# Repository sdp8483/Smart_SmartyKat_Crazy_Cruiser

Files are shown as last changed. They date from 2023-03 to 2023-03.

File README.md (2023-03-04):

# Smart SmartyKat Toy
## Modifying the SmartyKat Crazy Cruiser to be smarter about battery consumption

The Crazy Cruiser cat toy by SmartyKat is not so smart. The toy is the cat equivalent of a simple bristle bot. It consists of a power switch, LED, and vibration motor all powered by two LR44 coin cells. To activate the toy for cat play time a human is required to turn the toy on. During playtime it runs at a constant vibration speed and the light doesn't even blink! Not that smart. This also means that when kitty gets tired of playing (if a kitten can get tired please let me know) the toy will continue to run and drain the batteries. I aim to fix that by making the toy smarter.

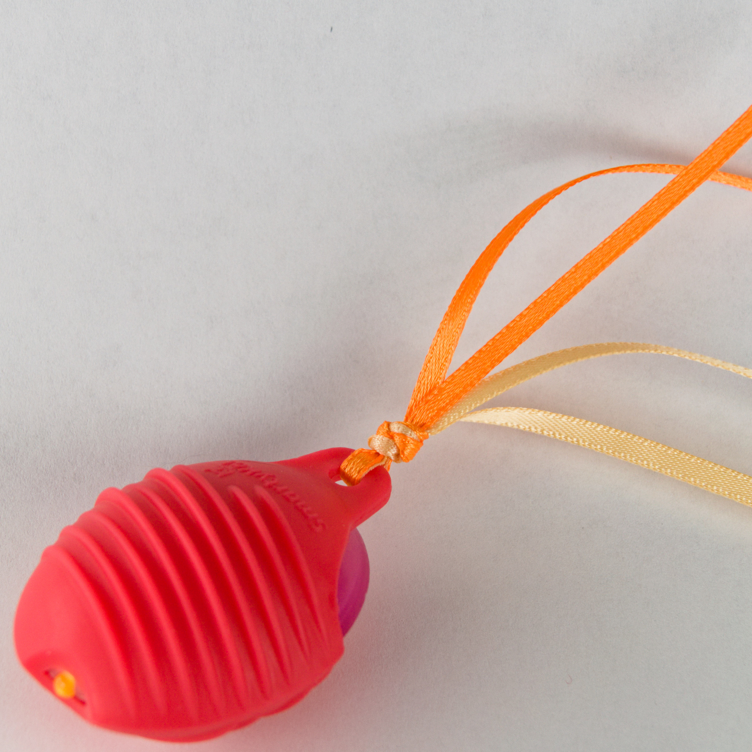
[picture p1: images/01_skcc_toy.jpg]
SmartyKat Toy


Simple and minimal parts will be used to smarten up this toy, after all it is still a low cost cat toy. This will be accomplished by adding a vibration switch and a microcontroller. The vibe switch will be used to wake up the uC from deep low power sleep in which the uC will start the vibration motor and LED. The toy will then remain active for a set amount of time then turn off to be activated later.

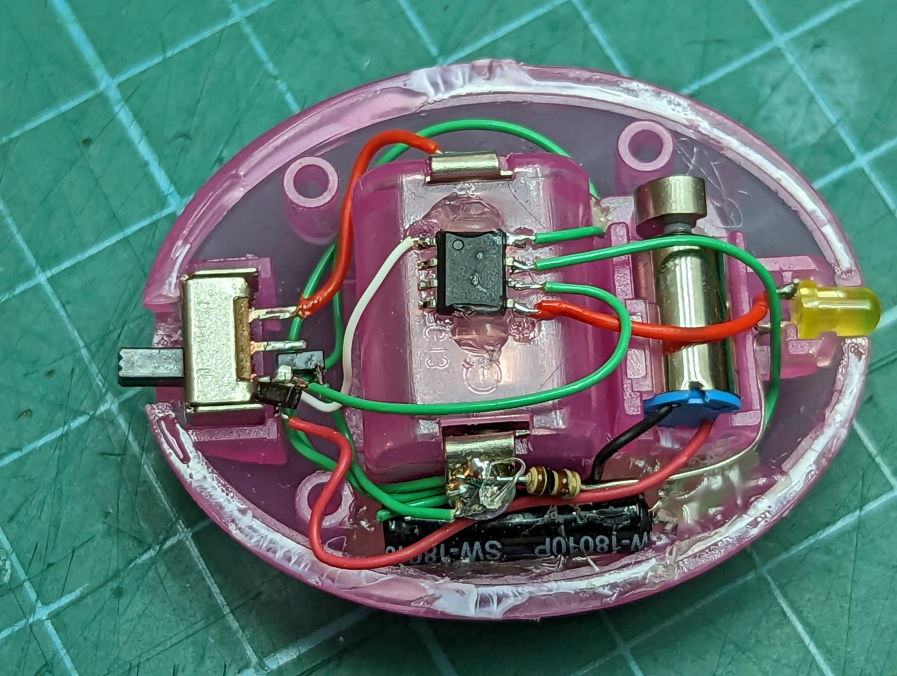
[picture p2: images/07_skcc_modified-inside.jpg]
Modified Toy


For more info see: https://samueldperry.com/2023/03/04/smart-smartykat-toy/

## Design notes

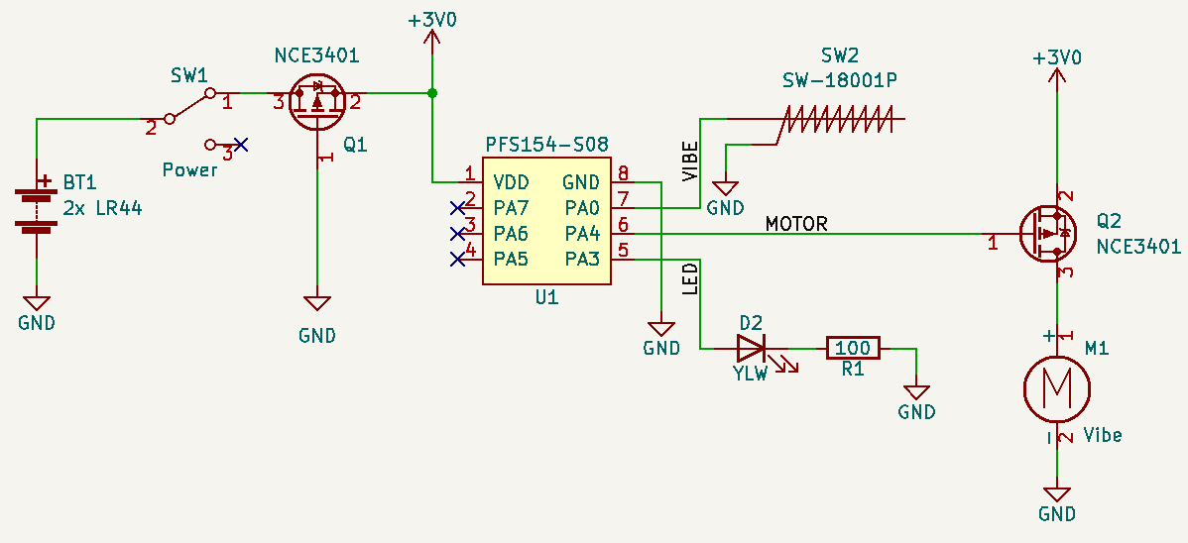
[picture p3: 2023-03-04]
pcb/images/skcc_schematic.png

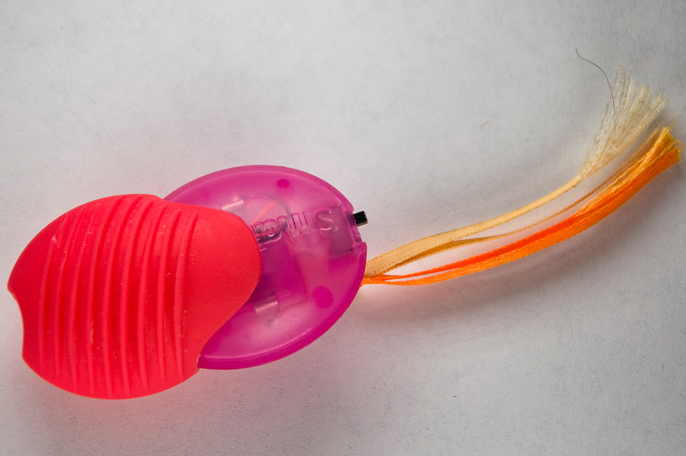
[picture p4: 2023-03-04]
images/02_skcc_toy.jpg

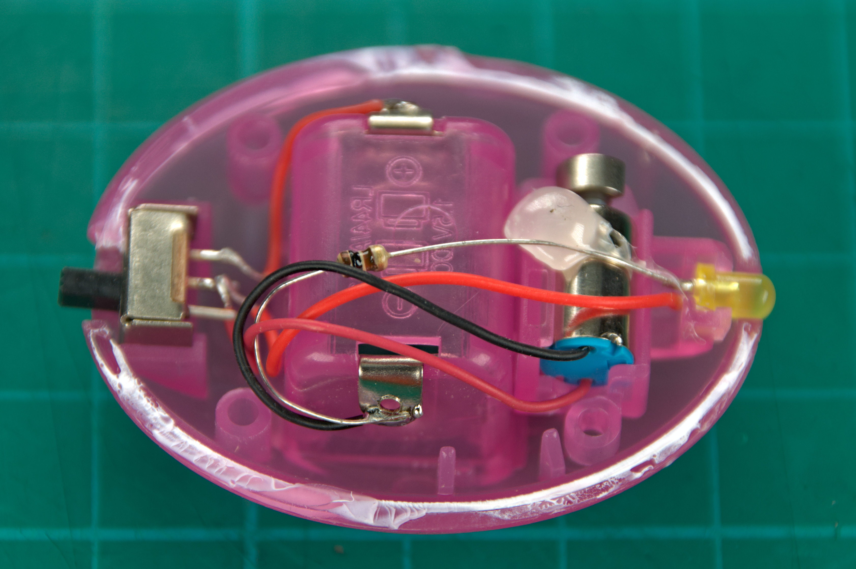
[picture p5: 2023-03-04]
images/03_skcc_stock-inside.jpg

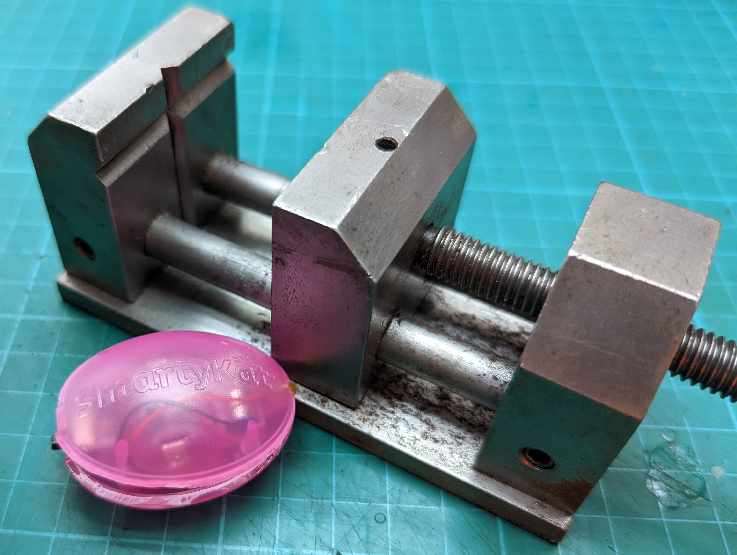
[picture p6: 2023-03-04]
images/04_skcc_craked-open.jpg

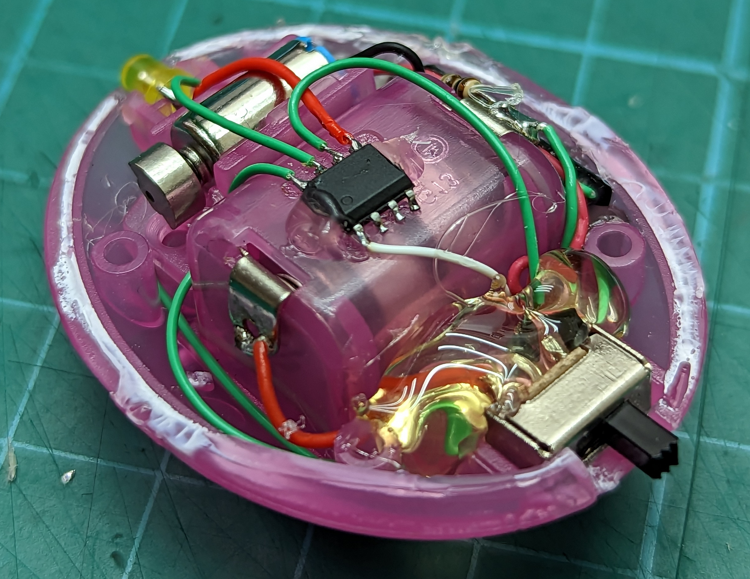
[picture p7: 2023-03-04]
images/08_skcc_hot-snot.jpg

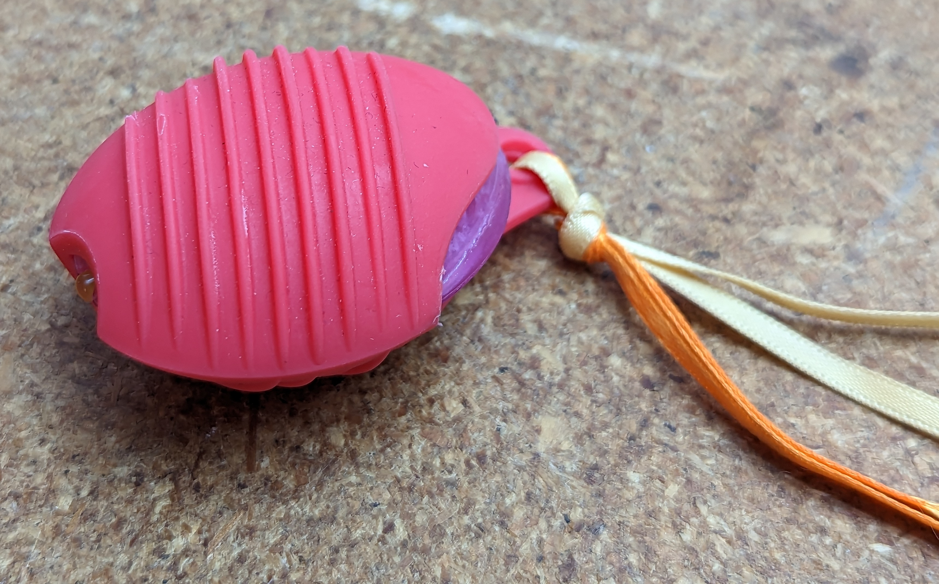
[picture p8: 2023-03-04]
images/09_skcc_done.jpg

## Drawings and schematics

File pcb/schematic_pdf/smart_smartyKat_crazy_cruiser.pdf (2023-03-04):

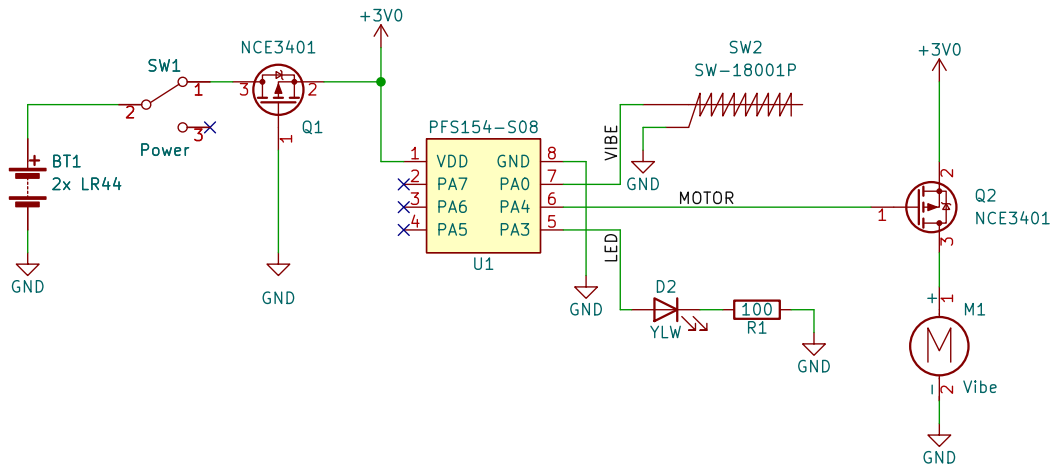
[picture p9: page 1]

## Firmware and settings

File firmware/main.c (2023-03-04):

/* Smart SmartyKat Crazy Cruiser
 * Target Device: PFS154-S08
 * 
 * Sam Perry 2023
 * github.com/sdp8483/Smart_SmartyKat_Crazy_Cruiser
 */

#include <stdint.h>
#include <pdk/device.h>
#include "auto_sysclock.h"

// Pin Defines - all pins are on port A
#define VIBE_PIN              0     /* vibration sensor input pin, used to wake from deep sleep */
#define MOTOR_PIN             4     /* motor control pin, controlled with a pmosfet */
#define LED_PIN               3     /* LED output pin, current source */

// Output Pin Fuction Defines
#define LED_ON()              PA |= (1 << LED_PIN)
#define LED_OFF()             PA &= ~(1 << LED_PIN)
#define LED_TOGGLE()          PA ^= (1 << LED_PIN)
#define MOTOR_ON()            PA &= ~(1 << MOTOR_PIN)
#define MOTOR_OFF()           PA |= (1 << MOTOR_PIN)


// Toggle the motor on and off to give toy some character using profiles
#define MAX_TICKS             64    /* go to sleep after this many ticks */
uint8_t tick = 0;                   /* tick count, number of T16 interrupts since starting T16 */
#define NUM_PROFILES          8     /* number of profiles, a new one is played each wake event to give more character */
uint64_t profile[NUM_PROFILES] = {0b1100110011001111111111000000000010101010101010101010111111111111,
                                  0b1111111111111111111111111111111111111111111111111111111111111111,
                                  0b1100110011001100110011001100110011111111111111111111111111111111,
                                  0b1111111111001111001111001111001111001111001111001111001111001111,
                                  0b0101010101010101010101010101010101010101010101010101010101010101,
                                  0b1111001110011100111001110011100111001110011100111001110011100111,
                                  0b1110111000000111000000000000000011111111111111111111111111111111,
                                  0b1110101010101010000000001111111101010101000000001111111101010101};
                                    /* motor will be turned on when bit is 1 and off when bit is 0 
                                       this playback profile is backwards */
uint8_t profile_i = 0;              /* profile number to playback, increments each wake */

// State Machine
typedef enum {
  GOTO_SLEEP,                       /* prepare to sleep */
  SLEEP,                            /* toy is in deep sleep */
  WAKEUP,                           /* toy was awaken from deep sleep */
  TOCK,                             /* T16 calling for next profile point */
  LIGHT_SLEEP,                      /* light sleep between ticks */
} fsm_states_t;

volatile fsm_states_t fsm_state = GOTO_SLEEP;

// Function Prototypes
void settling_delay(void);          /* use timer3 as delay to wait for vibe sensor to settle */

// Service Interrupt Requests
void interrupt(void) __interrupt(0) {
  /* Some notes and thoughts about interrupts on the PFS154
   *  Section 5.7 of the datasheet contains information about the interrupt controller.
   *  When an interrupt is triggered global interrupts are disabled, ie __disgint() is automaticaly called.
   *  CPU steps into ISR function below and executes code there. When done __engint() is automaticaly called and 
   *  code execution starts in the main loop where it left off. Confusingly the datasheet says that even if INTEN = 0 
   *  INTRQ can still be triggered by the interrupt source. So the peripheral or port should be further disabled to prevent
   *  triggering. */

  if (INTRQ & INTRQ_PA0) {          /* wake pin was pulled low */
    INTRQ &= ~INTRQ_PA0;            /* mark PA0 interrupt request serviced */
    fsm_state = WAKEUP;             /* change state */
  }

  if (INTRQ & INTRQ_T16) {          /* timer has expired */
    INTRQ &= ~INTRQ_T16;            /* mark T16 interrupt request serviced */
    T16C = 0;                       /* reset timer to zero */
    fsm_state = TOCK;               /* get next profile point */
  }

  if (INTRQ & INTRQ_TM2) {          /* LED toggle timer */
    INTRQ &= ~INTRQ_TM2;            /* mark interrupt request serviced */
    fsm_state = LIGHT_SLEEP;        /* go to light sleep */
  }

  if (INTRQ & INTRQ_TM3) {          /* settling delay has expired */
    INTRQ &= ~INTRQ_TM3;            /* mark interrupt request serviced */
  }
}

// Main program
void main() {
  MISC |= MISC_FAST_WAKEUP_ENABLE;  /* enable faster wakeup, 45 ILRC clocks instead of 3000 */

  // Initialize hardware
  PADIER = 0;                       /* on reset all pins are set as wake pins, setting register to 0 to disable */
  PBDIER = 0;                       /* there is no port B on the -S08 but without setting this to 0 the uC will wake unexpectedly */

  // Set Vibration Sensor pin as input
  PAC &= ~(1 << VIBE_PIN);          /* set as input (all pins are input by default, setting to make sure) */
  PAPH |= (1 << VIBE_PIN);          /* enable pullup resistor on pin */

  // Set output pins
  PAC |= (1 << MOTOR_PIN);          /* set motor control pin as output */
  PAC |= (1 << LED_PIN);            /* set led pin as output */
  LED_OFF();                        /* set initial LED state */
  MOTOR_OFF();                      /* set initial motor state */

  // Forever Loop
  while (1) {
    switch (fsm_state) {
      case GOTO_SLEEP:
        __disgint();                /* disable global interrupts */
        
        T16M = T16M_CLK_DISABLE;    /* turn off tick timer */
        TM2C = TM2C_CLK_DISABLE;    /* stop LED toggling */
        LED_OFF();
        MOTOR_OFF();

        settling_delay();           /* delay for vibe switch to settle */

        INTEN = 0;                  /* disable all interrupts */
        PADIER = (1 << VIBE_PIN);   /* enable only one wakeup pin */
        PBDIER = 0;                 /* make sure port B does not wake */
        INTEGS |= INTEGS_PA0_FALLING;
                                    /* trigger when switch closes and pulls pin to ground */
        INTEN |= INTEN_PA0;         /* enable interrupt on wake pin */
        INTRQ = 0;                  /* reset interrupts */

        fsm_state = SLEEP;          /* change state */
        break;

      case SLEEP:
        __engint();                 /* enable global interrupts */
        __stopsys();                /* go to deep sleep */
        break;
      
      case WAKEUP:
        __disgint();                /* disable global interrupts */
        INTEN = 0;                  /* disable all interrupts */
        PADIER = 0;                 /* disable wakeup pin */
        PBDIER = 0;                 /* disable port B wake pins to be sure */

        T16M = (uint8_t)(T16M_CLK_ILRC | T16M_CLK_DIV1 | T16M_INTSRC_13BIT);
                                    /* use 55kHz clock divided by 1, trigger when bit N goes from 0 to 1 
                                     * T16 is used as the tick count to determins playback of profile for motor */
        T16C = 0;                   /* set timer count to 0 */
        INTEN |= INTEN_T16;         /* enable T16 interrupt */
        INTRQ = 0;                  /* reset interrupts */

        // use timer2 to toggle LED
        TM2C = (uint8_t)(TM2C_CLK_ILRC | TM2C_OUT_PA3 | TM2C_MODE_PERIOD);
        TM2S = (uint8_t)(TM2S_PRESCALE_DIV4 | TM2S_SCALE_DIV3);
        TM2B = 250;                 /* set timer frequency to 6.8Hz */
        INTEN |= INTEN_TM2;         /* enable timer2 interrupt */

        tick = 0;                   /* reset tick count to reset profile playback */
        fsm_state = TOCK;           /* change state to set motor playback from profile */
        break;
      
      case TOCK:
        __disgint();                /* dont interrupt during tock */
        if (tick >= MAX_TICKS) {    /* done playing? time for sleep */
          profile_i++;              /* play next profile on wake */
          profile_i = (profile_i > (NUM_PROFILES - 1)) ? 0 : profile_i;
                                    /* constrain profile_i */
          fsm_state = GOTO_SLEEP;   /* change state, go to sleep */
          break;                    /* don't execute remainder of code */
        }

        // get motor state in profile playback based on tick number
        if (((profile[profile_i] >> tick) & 0b01) == 1) { 
          MOTOR_ON();
        } else {
          MOTOR_OFF();
        }

        tick++;                     /* increment tick */

        __engint();                 /* enable global interrupts */
        __stopexe();                /* light sleep, ILRC remains on */
        break;

      case LIGHT_SLEEP:
        __engint();                 /* enable global interrupts */
        __stopexe();                /* light sleep, ILRC remains on */
        break;

      default:
        fsm_state = GOTO_SLEEP;     /* something is wrong, go to sleep */
        break;
    }
  }
}
// Use timer3 to delay while vibration sensor settles
void settling_delay(void) {
  TM3C = (uint8_t)(TM3C_CLK_ILRC | TM3C_OUT_DISABLE | TM3C_MODE_PERIOD);
  TM3S = (uint8_t)(TM3S_PWM_RES_8BIT | TM3S_PRESCALE_DIV4 | TM3S_SCALE_DIV13);
                              /* setup for 0.256sec period */
  TM3B = 250;                 /* timer3 counts up to this value before interrupting */
  INTEN |= INTEN_TM3;         /* enable interrupt for timer3 */
  __engint();                 /* enable global interrupts */
  LED_ON();                   /* to see that delay is happening */
  __stopexe();                /* light sleep for a delay */
  LED_OFF();                  /* delay is done */

  __disgint();                /* disable global interrupts */
  TM3C = TM3C_CLK_DISABLE;    /* disable timer */
}

// Startup code - Setup/calibrate system clock
unsigned char _sdcc_external_startup(void) {
  /* Set the system clock 
   * note it is necessary to enable IHRC clock while updating clock settings or CPU will hang  */
  PDK_USE_ILRC_SYSCLOCK();          /* use ILRC 55kHz clock as sysclock */
  PDK_DISABLE_IHRC();               /* disable IHRC to save power */
  EASY_PDK_CALIBRATE_ILRC(F_CPU, TARGET_VDD_MV);

  return 0;   // Return 0 to inform SDCC to continue with normal initialization.
}

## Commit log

2023-02-19 init commit
    [smart_smartyKat_crazy_cruiser.kicad_pcb, smart_smartyKat_crazy_cruiser.kicad_sch]
2023-02-19 everything happens in interrupts
2023-02-19 allow fuse setting
2023-02-25 PWM motor
2023-02-26 remove pwm, use playback
2023-02-26 reset tick so it will wake again
    [main.c]
2023-02-26 motor switch with NPN, change on off defines
2023-02-26 toggle LED with Timer2
2023-02-26 remove led toggle with Timer2
    timer2 wakes and disrupts tick timing with Timer16
2023-02-26 put timer2 delay in function
2023-02-26 motor control with pmosfet
2023-02-26 actually use timer3 as settling delay
2023-02-27 bug fixes
    fsm_state set to volatile
    TM2 has a INTRQ
    dont interrupt TOCK
    [main.c]
2023-03-04 simplify schema
    [smart_smartyKat_crazy_cruiser.kicad_sch]
